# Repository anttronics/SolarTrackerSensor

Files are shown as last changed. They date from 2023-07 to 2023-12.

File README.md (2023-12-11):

## SolarTrackerSensor
A simple sensor circuit that uses photo-transistors and boolean logic to indicate if a solar panel is pointing straight at the sun. 

### Outputs 
- It produces 4 digital outputs to indicate if movement is required in up, down, left or right directions. Those outputs can be passed directly to a motor controller which can correct the mis-alignment. 
- It also produces horizontal, vertical and combined "busy" signals to allow independent, as well as overall enabling/disabling of the motors.

**Warning**: All outputs are unprotected, digital signal outputs and should not be used to drive any motors directly.

### Limit Switches
It has normally-closed (NC) limit switch inputs for all 4 directions, but requires at least the "east" and "down" switches for auto-parking to function. The "west" and "up" limit switches can be omitted/bypassed if the motion mechanism has sufficient range and/or limits implemented elsewhere.

### Auto-parking
When the ambient light level falls below the adjustable threshold, it will auto-park the panel in the "east" and "down" position. Without the auto-park function, in the summer months, the panel would be left pointing west at sunset. The sun would then rise behind the panel and tracking would not resume until late morning, when the sun moves n front of the panel again.

### Sensitivity
A common reference level for all 4 comparators is produced using a potentiometer as a voltage divider. The simplest way to set the sensitivity is to adjust it on a dark cloudy day, to a level just above the parking level. This way it won't try to auto-park the panel every time a cloud moves across the sun. 

### Assembly
The board is designed in 3 parts: 
- the "logic" part which contains all the main components,
- the "sensor" part which contains the photo-transistors and
- the "shield" parts. 

The "sensor" board has the same footprints on both sides, allowing assembly on the "N" or "S" side, depending on whether the sun will be tracked from the north or south hemisphere.

It can be separated from the "logic" board and connected with wires, or it can be kept attached to the "logic" board. The traces between the boards complete all the required connections between the two boards.

The "shield" parts, when soldered onto the "sensor" board, form a pyramid-shaped sun screen that cast a shadow on the photo-transistors when the panel is not correctly aligned.

### Power supply
Even though all the components on the board could handle a higher voltage, a stable 5V DC power supply is highly recommended to ensure the reference levels for the comparator are actually effective. 

### Future ideas
- Motor control board with sleep/periodic wake-up function for low power consumption
- Battery charging board with constant panel voltage or MPP tracking.

### How did we get here?
The prototype "ancestor" of this board has been keeping an A4-size 4V panel pointed at the sun through my office window for a few years already. It charges a 2S LiPo battery during the day which in turn is used as a power bank to charge my phone. 

The mechanical construction is showing its age and needs an overhaul. The plan is to switch from continuous rotation servos to DC gear motors for smoother movement and in the process, try to tidy up the electronics as well.

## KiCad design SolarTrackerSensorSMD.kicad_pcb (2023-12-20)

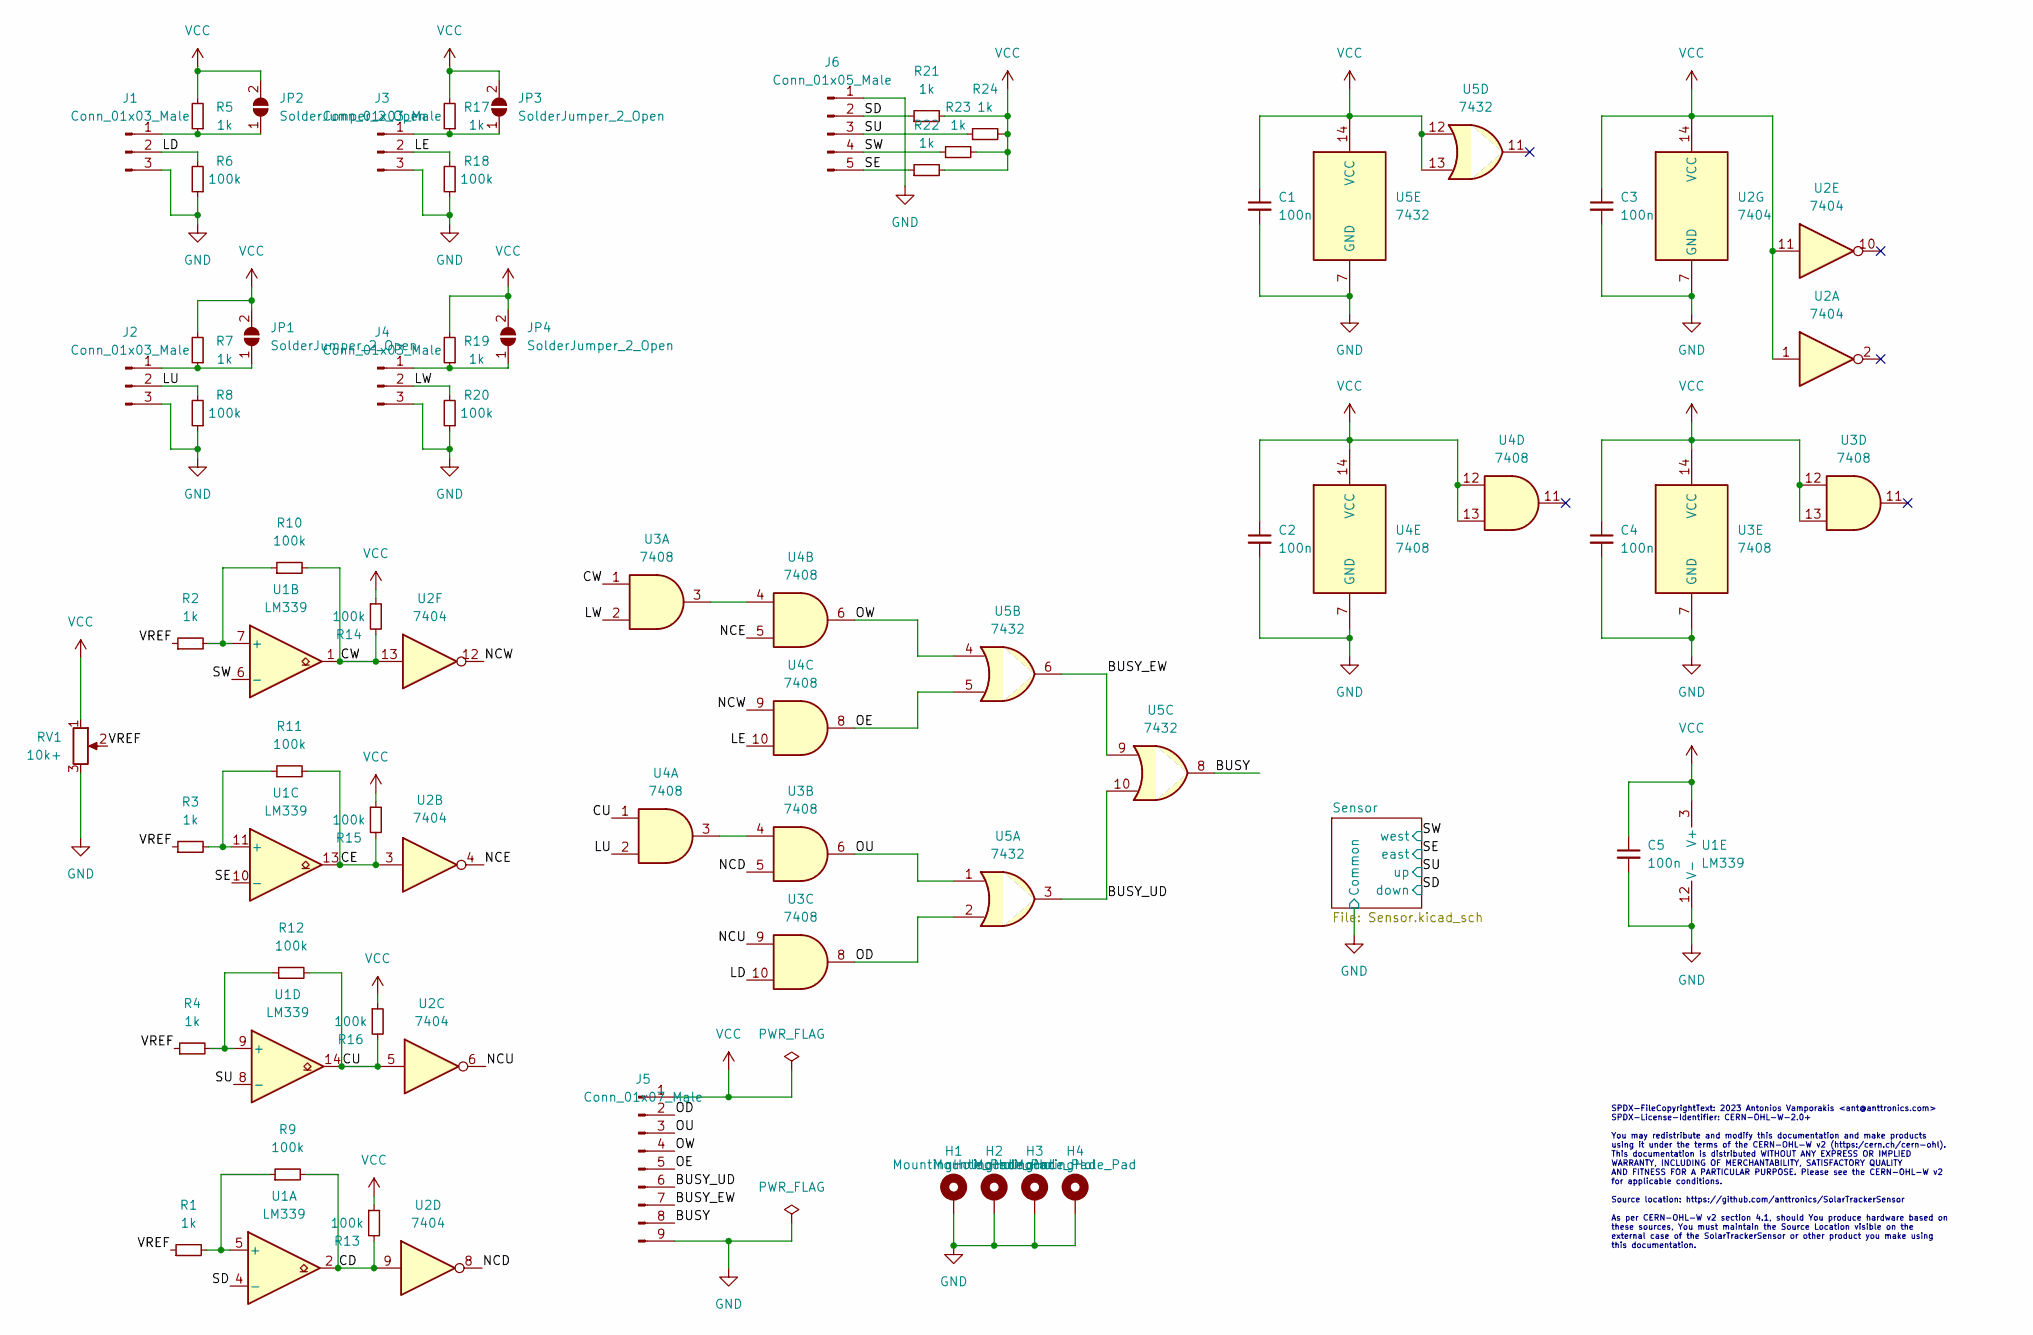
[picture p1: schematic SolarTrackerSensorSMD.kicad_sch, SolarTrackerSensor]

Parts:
C1, C2, C3, C4, C5: 100n; C_0603_1608Metric; MPN C282519
H1, H2, H3, H4: MountingHole_Pad; MountingHole_3.2mm_M3_DIN965_Pad
J1, J2, J3, J4: Conn_01x03_Male; PinHeader_1x03_P2.54mm_Vertical
J5: Conn_01x07_Male; PinHeader_1x09_P2.54mm_Vertical
J6: Conn_01x05_Male; PinHeader_1x05_P2.54mm_Vertical
JP1, JP2, JP3, JP4: SolderJumper_2_Open; SolderJumper-2_P1.3mm_Open_RoundedPad1.0x1.5mm
R1, R2, R3, R4, R5, R7, R17, R19, R21, R22, R23, R24: 1k; R_0603_1608Metric; MPN C3152127
R6, R8, R9, R10, R11, R12, R13, R14, R15, R16, R18, R20: 100k; R_0603_1608Metric; MPN C2907088
RV1: 10k+; Potentiometer_Bourns_3296W_Vertical; MPN C118963
U1: LM339; SOIC-14_3.9x8.7mm_P1.27mm; MPN C5456631
U2: 7404; SOIC-14_3.9x8.7mm_P1.27mm; MPN C141316
U3, U4: 7408; SOIC-14_3.9x8.7mm_P1.27mm; MPN C337768
U5: 7432; SOIC-14_3.9x8.7mm_P1.27mm; MPN C132988

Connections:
/BUSY: J5.8, U5.8
/BUSY_EW: J5.7, U5.6, U5.9
/BUSY_UD: J5.6, U5.3, U5.10
/CD: R9.2, R13.2, U1.2, U2.9
/CE: R11.2, R15.2, U1.13, U2.3
/CU: R12.2, R16.2, U1.14, U2.5, U4.1
/CW: R10.2, R14.2, U1.1, U2.13, U3.1
/LD: J1.2, R6.2, U3.10
/LE: J3.2, R18.2, U4.10
/LU: J2.2, R8.2, U4.2
/LW: J4.2, R20.2, U3.2
/NCD: U2.8, U3.5
/NCE: U2.4, U4.5
/NCU: U2.6, U3.9
/NCW: U2.12, U4.9
/OD: J5.2, U3.8, U5.2
/OE: J5.5, U4.8, U5.5
/OU: J5.3, U3.6, U5.1
/OW: J5.4, U4.6, U5.4
/SD: J6.2, R21.1, U1.4 (-); also elsewhere on the board
/SE: J6.5, R22.1, U1.10 (-); also elsewhere on the board
/SU: J6.3, R24.1, U1.8 (-); also elsewhere on the board
/SW: J6.4, R23.1, U1.6 (-); also elsewhere on the board
/VREF: R1.1, R2.1, R3.1, R4.1, RV1.2
GND: C1.2, C2.2, C3.2, C4.2, C5.2, H1.1, H2.1, H3.1, H4.1, J1.3, J2.3, J3.3, J4.3, J5.9, J6.1, R6.1, R8.1, R18.1, R20.1, RV1.3, U1.12 (V-), U2.7 (GND), U3.7 (GND), U4.7 (GND), U5.7 (GND); also elsewhere on the board
unnamed: J1.1, JP2.1 (A), R5.1
unnamed: J2.1, JP1.1 (A), R7.1
unnamed: J3.1, JP3.1 (A), R17.1
unnamed: J4.1, JP4.1 (A), R19.1
unnamed: R1.2, R9.1, U1.5 (+)
unnamed: R2.2, R10.1, U1.7 (+)
unnamed: R3.2, R11.1, U1.11 (+)
unnamed: R4.2, R12.1, U1.9 (+)
unnamed: U3.3, U4.4
unnamed: U3.4, U4.3
VCC: C1.1, C2.1, C3.1, C4.1, C5.1, J5.1, JP1.2 (B), JP2.2 (B), JP3.2 (B), JP4.2 (B), R5.2, R7.2, R13.1, R14.1, R15.1, R16.1, R17.2, R19.2, R21.2, R22.2, R23.2, R24.2, RV1.1, U1.3 (V+), U2.1, U2.11, U2.14 (VCC), U3.12, U3.13, U3.14 (VCC), U4.12, U4.13, U4.14 (VCC), U5.12, U5.13, U5.14 (VCC)

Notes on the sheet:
SPDX-FileCopyrightText: 2023 Antonios Vamporakis <ant@anttronics.com> SPDX-License-Identifier: CERN-OHL-W-2.0+ You may redistribute and modify this documentation and make products using it under the terms of the CERN-OHL-W v2 (https:/cern.ch/cern-ohl). This documentation is distributed WITHOUT ANY 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

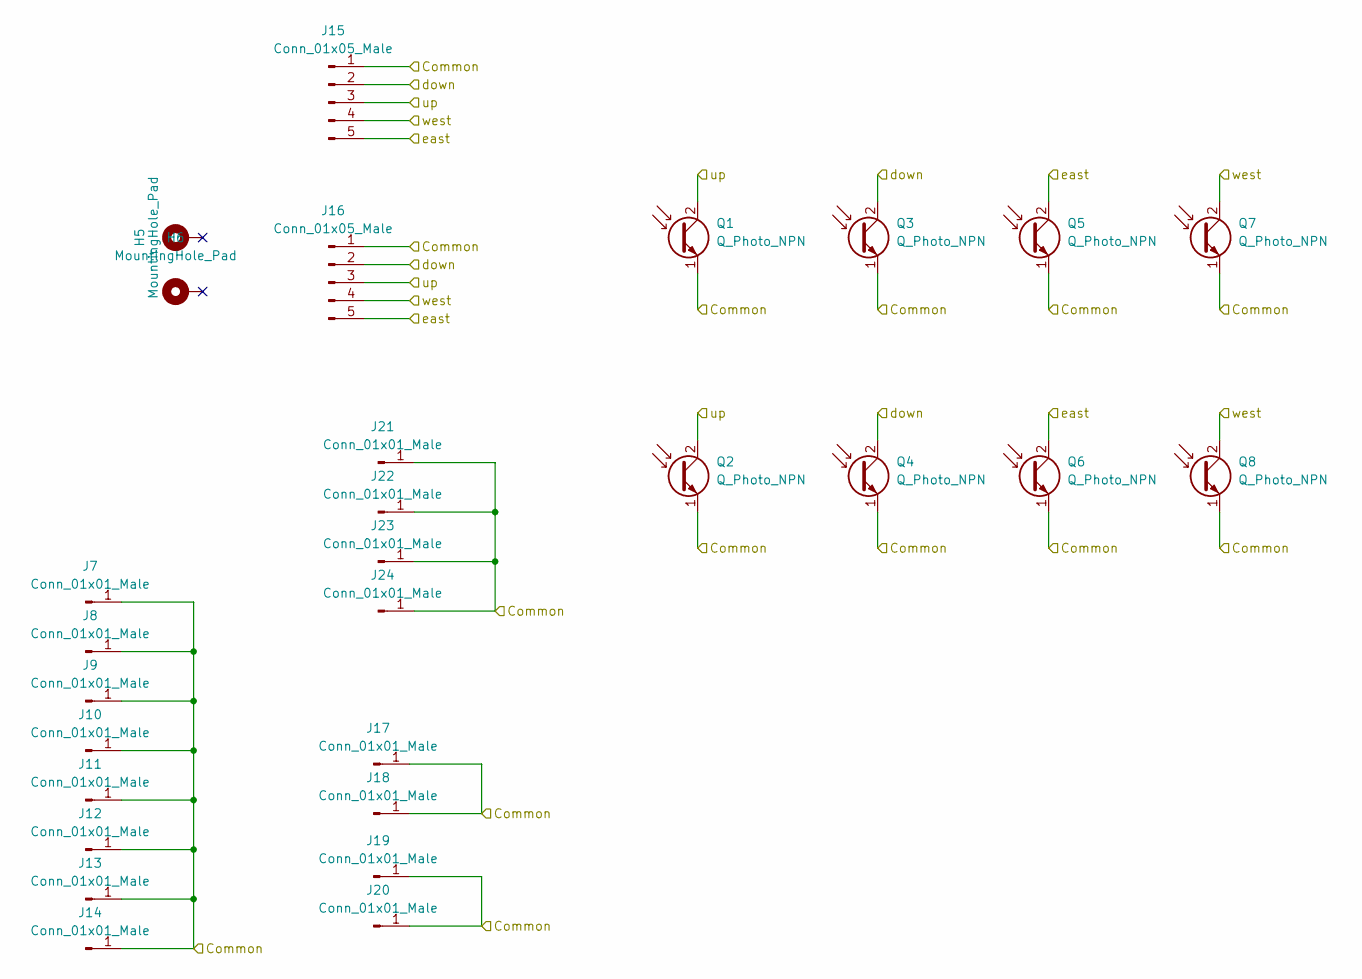
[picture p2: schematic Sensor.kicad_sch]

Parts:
H5, H6: MountingHole_Pad; MountingHole_3.2mm_M3_DIN965_Pad
J7, J8, J9, J10, J11, J12, J13, J14: Conn_01x01_Male; TestPoint_Pad_4.0x4.0mm
J15, J16: Conn_01x05_Male; PinHeader_1x05_P2.54mm_Vertical
J17, J18, J19, J20: Conn_01x01_Male; TestPoint_Pad_D4.0mm
J21, J22, J23, J24: Conn_01x01_Male; TestPoint_THTPad_D4.0mm_Drill2.0mm
Q1, Q2, Q3, Q4, Q5, Q6, Q7, Q8: Q_Photo_NPN; LED_0603_1608Metric; MPN C146233

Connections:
/SD: J15.2, J16.2, Q3.2 (C), Q4.2 (C); also elsewhere on the board
/SE: J15.5, J16.5, Q5.2 (C), Q6.2 (C); also elsewhere on the board
/SU: J15.3, J16.3, Q1.2 (C), Q2.2 (C); also elsewhere on the board
/SW: J15.4, J16.4, Q7.2 (C), Q8.2 (C); also elsewhere on the board
GND: J7.1, J8.1, J9.1, J10.1, J11.1, J12.1, J13.1, J14.1, J15.1, J16.1, J17.1, J18.1, J19.1, J20.1, J21.1, J22.1, J23.1, J24.1, Q1.1 (E), Q2.1 (E), Q3.1 (E), Q4.1 (E), Q5.1 (E), Q6.1 (E), Q7.1 (E), Q8.1 (E); also elsewhere on the board

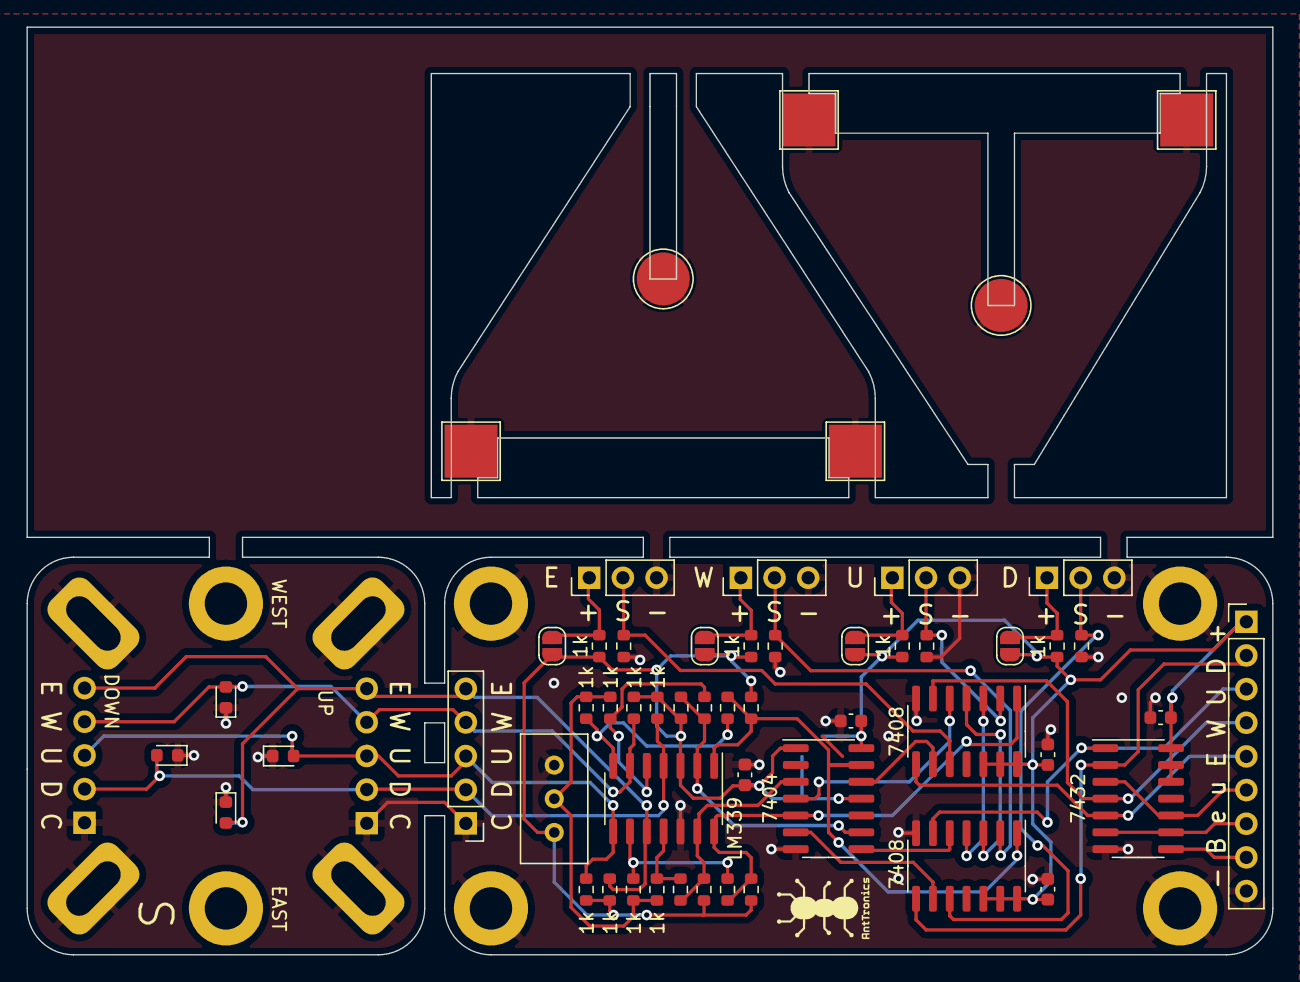
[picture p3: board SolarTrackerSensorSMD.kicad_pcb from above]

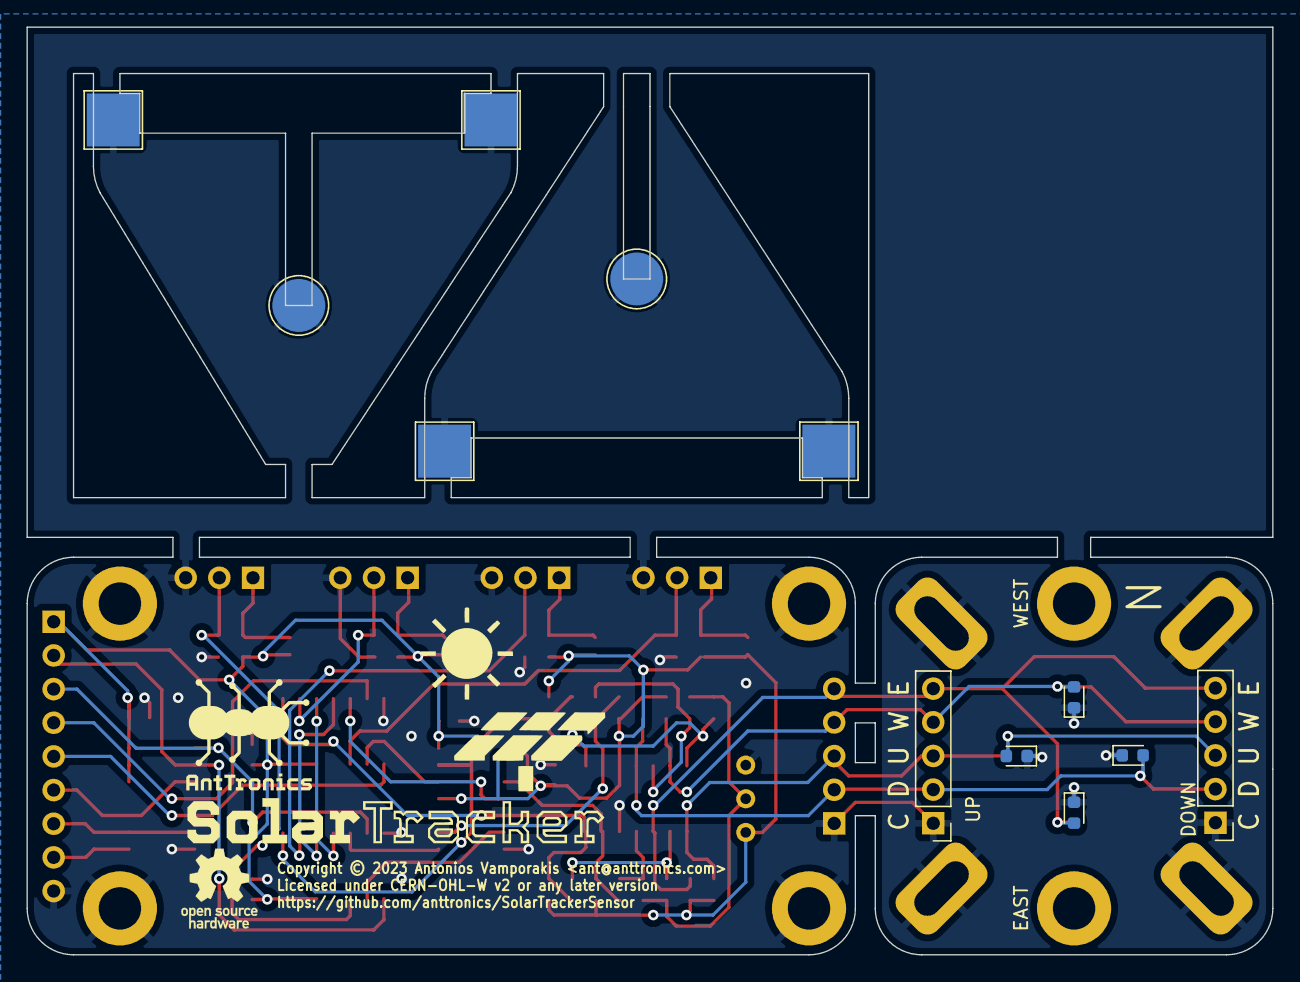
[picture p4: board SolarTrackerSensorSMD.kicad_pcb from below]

Board: 2 copper layers, 94.0 x 70.0 mm, 77 parts (12 on the bottom side), 36 nets.

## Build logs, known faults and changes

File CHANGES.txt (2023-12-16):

Anyone modifying the design should provide brief information about the 
modifications, including the date they were made.  

Information about the design should be added but never removed from this
file. According to section 3.3.b of the licence, licensees should
provide a brief entry with a date and the nature of the modification for
each design change. For example ‘2020-04-26: AC/DC power converter
circuit removed as AC input no longer necessary’.

2023-06-01 Initial Version
2023-07-08 Replace Idle signal with Busy_UD & Busy_EW

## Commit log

2023-07-08 Replace Idle with Busy_UD & Busy_EW
    [SolarTrackerSensorSMD.kicad_pcb, SolarTrackerSensorSMD.kicad_sch]
2023-12-11 Remove loose schematic
    [Sensor.kicad_sch]
2023-12-14 restore Sensor.kicad_sch
    [Sensor.kicad_sch]
2023-12-16 Add licence & reshuffle silkscreen graphics
    [SolarTrackerSensorSMD.kicad_pcb, SolarTrackerSensorSMD.kicad_sch]
2023-12-20 CERN OHL W seems more appropriate
    [SolarTrackerSensorSMD.kicad_pcb, SolarTrackerSensorSMD.kicad_sch]

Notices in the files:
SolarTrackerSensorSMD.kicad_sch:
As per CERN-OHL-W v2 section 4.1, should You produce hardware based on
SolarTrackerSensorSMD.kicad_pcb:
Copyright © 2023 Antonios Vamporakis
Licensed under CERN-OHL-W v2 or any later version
